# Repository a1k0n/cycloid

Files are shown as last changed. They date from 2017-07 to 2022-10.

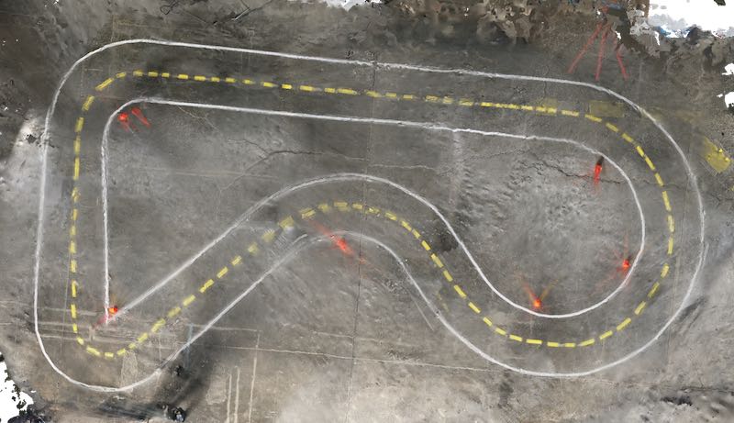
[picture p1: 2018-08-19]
design/coneslam/trackmap.jpg

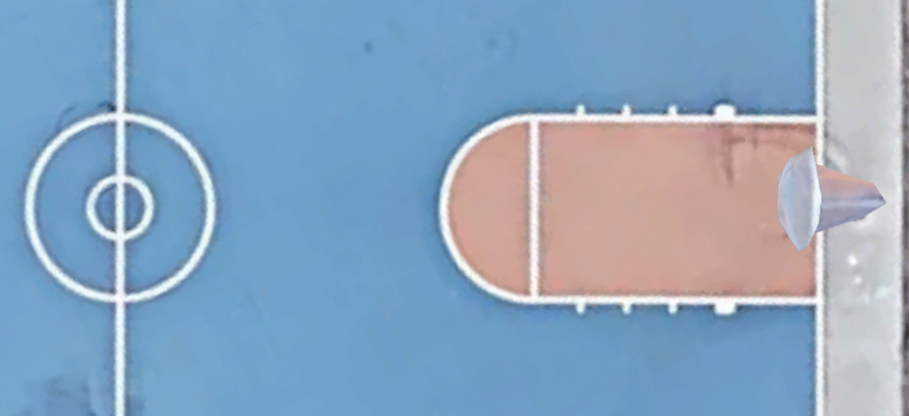
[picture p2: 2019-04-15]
design/trackplan/bball-2cm.png

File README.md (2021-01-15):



Self-racing robot using either ceiling lights or traffic cones to localize.
Very much a work in progress and documentation will always be severely
lacking as this is a constantly moving target!

This is my ongoing entry in the quarterly [DIY Robocars
competition](https://diyrobocars.com/") in Oakland, CA.

Cycloid at CircuitLaunch in Oakland (https://www.youtube.com/watch?v=vWJduGcik6Q)

## Hardware (updated!)

I've switched to a 1/10th scale touring car (for flat ground courses) as it
handles much better and also eliminates the very finicky wheel encoders used on
the Rustler.

Touring car:

 - HobbyKing Blaze R2 ($99)
 - Turnigy TrackStar 9.5T sensored brushless motor 4120KV ($34)
 - Turnigy TrackStar 80A brushless sensored ESC ($40)
 - TrackStar TS-411MG digital servo ($17)
 - Basher 6600mAh 2S2P 40C hardcase LiHV pack ($38) (smaller batteries are
   fine, but I like being able to run the computer all day on one charge)
 - Tires appropriate for track (Schumacher Racing SST Mini Pins are the way to go on carpet)

Electronics:

 - Raspberry Pi 3 B ($35)
 - SanDisk Ultra 32GB microSDHC UHS-I Card ($9) -- it's important to have the
   right kind of SD card or it won't keep up with recordings, and it's hard to
   tell ahead of time which ones will work.
 - Arducam OV5647 Raspberry Pi 3 camera with LS-40180 fisheye lens ($30)
 - ILI9340 SPI 240x320 LCD display, via the fbtft device driver (about $7)
 - Some XT60 plugs and an extra 6-wire brushless sensor cable (~$10)
 - Logitech F710 wireless game pad w/ USB dongle (~$40)
 - Custom HAT board w/ STM32F030 and ICM-20600 IMU: https://easyeda.com/a1k0n/cycloid (PCB +
   parts is about $5 apiece in qty 10 from JLPCB / LCSC, plus you have to
   solder it all together)

Total hardware cost for the car comes to under $350, plus the cost of the
wireless controller (~$40).

### 3D printed mounting parts

Besides the RC car, there are three 3D-printed parts to mount the camera and
electronics for various cars (Blaze R2, Traxxas Rustler, Exceed Magnet,
WLToys K989). I drill and tap 2.5mm screw holes in most of them. These are
all modeled in OpenSCAD and source code and .stl files are in `hw/scad/`.

### Configurations

There is a mandatory configuration file called `cycloid.ini` which allows you
to specify the mode of communication to the ESC and servos (Cycloid HAT
board, GPIO pins supported; code also exists for Teensy and PCA9685) as well
as specify which IMU (all Invensense MPU-9x50, MPU-6050, ICM-2060x supported)

See `cycloid.ini.example` for full details.

### Defining a race track

 - `tools/ceilslam` has code to turn a datalog saved from the car into a
 birds-eye view of the track based on ceiling light tracking and reprojecting
 the pixels which can see the floor.

 - `tools/trackplan/gui.py` contains a Dear Imgui-based application for
 defining a racetrack boundary (and cone locations) given a birdseye view of
 the track. It can also get a birdseye view of the track given two different
 views and matching sets of points.

## Code

Can be compiled on a host PC with a cross compiler (e.g. on macOS you can
install this: https://www.jaredwolff.com/toolchains/) or on the Raspberry Pi
itself.

If you want to build the code, clone with `git clone --recursive
https://github.com/a1k0n/cycloid` in order to get the Raspberry Pi userland
submodule (otherwise just run `git submodule init` and `git submodule update`).

Here's how I build it:

Once you have a raspberry pi cross compiler (see two paragraphs above), edit
`crosscompile.cmake` to point to the correct compiler name / path, and do this:

```
$ mkdir build
$ cd build
$ cmake -DCMAKE_TOOLCHAIN_FILE=../crosscompile.cmake ../src -DCMAKE_BUILD_TYPE=RelWithDebInfo
$ make -j4
```

The main executable will be in `build/drive/drive`; scp that to your raspberry
pi on the car, create a `cycloid.ini`, pair a joystick, and run it.

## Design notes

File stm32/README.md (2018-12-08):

# Cycloid STM32 code

This code was mostly generated by the STM32CubeMX utility; the actual code that
does anything is in Src/main.c.

This code is for the Cycloid HAT board: https://easyeda.com/a1k0n/cycloid

It exposes an I2C device on address 0x75 and is also available via the serial
port; in fact, it will send a heartbeat on the serial port every 10ms, just as
it generates the PWM pulse for the servo and speed controller. This way, a
control loop on the Raspberry Pi can be synchronized with the actual pulses
sent to the car hardware.

## Compiling the code

Install `arm-none-eabi-gcc` on your host platform and type `make`. Copy
build/cycloidp1.1.elf to the Pi and you can flash it right on there.

## Flashing the code

The Raspberry Pi can reflash the code on the HAT using
[OpenOCD](http://openocd.org/). Raspbian has an `openocd` package, but it isn't
new enough to work using the Pi's own GPIO pins. Adafruit has a [guide to
compiling
OpenOCD](https://learn.adafruit.com/programming-microcontrollers-using-openocd-on-raspberry-pi/compiling-openocd)
which will get you up to speed. Once you have it installed, use the
`openocd.cfg` here (or modify it for your needs; it's looking for
`cycloidp1.1.elf` in the current working directory) and `sudo openocd -f openocd.cfg`. If you see
```
...

** Verify Started **
verified 8348 bytes in 0.035556s (229.282 KiB/s)
** Verified OK **
adapter speed: 1001 kHz
Info : Listening on port 6666 for tcl connections
Info : Listening on port 4444 for telnet connections
```

then it worked, and you can hit ^C, or if you really want to you can connect up
gdb and poke around.

## I2C addresses

`i2cdump 1 0x75` will show the "registers" exposed by the I2C slave; the first
three addresses can be written to. The `i2cset` / `i2cget` utilities also work.

| Address | Datatype | Function | Read/write |
|-|-|-|-|
| 0x00 | uint8 | Bits 0 and 1 are the red and green LEDs | R/W |
| 0x01 | int8 | Servo position, (-128..127) | R/W |
| 0x02 | int8 | Speed controller position, (-128..127) | R/W |
| 0x03-0x04 | uint16 little-endian | Cumulative motor encoder ticks | R |
| 0x05-0x06 | uint16 little-endian | Motor period, microseconds per tick or 0 if stopped | R |

There are three "encoder ticks" per motor revolution (it's counting the falling
edge of each of the three motor phase windings).

Cumulative encoder ticks wraps at 65536, naturally; just subtract the previous
reading from the current one to get the number of ticks since last reading.
This can be used to determine distance travelled (divide by 3\*total gear ratio,
multiply by wheel circumference).

Motor period gives you the inverse motor velocity; if the field is nonzero,
divide 1000000 / period to get velocity in ticks/second.

## Serial format

The serial protocol sends a 6-byte packet every 10ms at 115200 baud, 8 data
bits, 1 stop bit, no parity:

| Offset | Value | Description |
|-|-|-|
| 0 | 0xAA | sync marker |
| 1-2 | motor encoder ticks (uint16le) | same as address 0x03-0x04 from I2C registers |
| 3-4 | motor encoder period (uint16le) | same as address 0x05-0x06 from I2C registers |
| 5 | checksum | one's complement of sum of bytes 0..4 |

It accepts 5-byte packets:

| Offset | Value | Description |
|-|-|-|
| 0 | 0x55 | Sync marker |
| 1 | LED flags | same as address 0x00 in I2C registers |
| 2 | servo position (int8) | same as address 0x01 |
| 3 | ESC position (int8) | same as address 0x02 |
| 4 | checksum | one's complement of sum of bytes 0..3 |

If the receiver's checksum doesn't match, it will respond with 0xFE (if it was
not already transmitting a packet; otherwise it will silently ignore the input)

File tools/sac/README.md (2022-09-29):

# soft actor-critic implementation for diyrobocars

trains 2x *Q* networks and one &pi; network.

the network architecture has an embedding layer like a language model has; one
*d*-dim vector for each point on the track. Track data is a side input
containing x, y of centerline and unit vector pointing forward along the track.
The Circuit Launch track this was initially trained on has 315 points,
subdivided roughly equidistantly from an SVG drawing.

So each little spot on the track is kind of like a token in a language model,
so that the network can learn the optimal way through the track at that
particular spot.

The embedding is added to the local state [x, y in local track frame, sin/cos
of direction in local track frame, velocity, yaw rate] projected through a
linear layer.

```
 [state vector]                              [action (Q network only)]
----------------                                 ---------------
| linear 6 x H |      [track embedding, dim=H]   | linear 2 x H|
       |                        |                   |
       `----------(+)-----------'-------------(+)---'
                   |
            |Mish activation|
                   |
            |   HxH linear  |
                   |
            |Mish activation|
                   |
         .-----------------------------------.
         |                |                  |
   | linear Hx2 |   | linear Hx2 |     | linear Hx1 |
      action mu     action logstd          Q value
  |-------pi network only--------|  |-Q networks only-|
```

The *Q* network has 128 hidden dimensions; the &pi; network has 16.

So basically, I just add the track embedding to the projection of the state
(/action as applicable), mish activation, run it through a fully-connected
layer, another mish activation, then a linear projection to get actions or Q
values. The architecture is extremely simple because the control policy is
locally extremely simple; the embedding layer contains all the information on
the best racing line.

There is an alternative, more general way to do this that wouldn't be
map-specific, which is to feed the future curvature information into the
network as an input.

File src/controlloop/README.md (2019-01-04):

this code uses the new serial interface to the STM32F030 HAT board to make a
lock-step 100Hz control loop.

experimental only for now; will roll this into drive/ soon.

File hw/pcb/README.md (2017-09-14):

This is a PCB which carries the Teensy 3.2 and connects to the servo & speed
controller on the car, as well as the stock R/C radio, wheel encoders, and an
analog feedback tap from the servo's internal potentiometer (requires modifying
servo).

It has the same mounting holes as the PCA9685 I2C PWM expander board commonly
used for the purpose of connecting a Raspberry Pi to an R/C car.

It can be seen (and purchased) here: 


<br>
<a href="https://oshpark.com/shared_projects/DP0wzTcU">order on OSHPark</a>

(Note that I have a ton of extras; if you ask me at an Oakland DIYRobocars race
I'll give you one)

It also has an i2c piggyback connection for the IMU.

R1 and R2 are pull-up resistors for I2C; I do not recommend populating them,
however.

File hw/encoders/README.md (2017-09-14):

Wheel encoders are jleichty's design:

http://www.blargh.co/2013/12/rc-car-quadrature-wheel-encoders.html

Except I'm only using one of the two encoder channels on each wheel, as I
assume wheels only go forwards.

PCBs are available at https://www.oshpark.com/profiles/jleichty

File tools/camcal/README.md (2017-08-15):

I use a 170 degree fisheye camera (this model:
https://www.amazon.com/dp/B01FR03MGG )

so this is a fisheye calibration

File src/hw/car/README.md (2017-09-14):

Interfacing code with RC car components.

Supports PCA9685 (not currently used) and a Teensy communicating via I2C,
running the code in the `arduino` code directory at the top level of this
repository.

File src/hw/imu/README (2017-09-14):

IMU is 3 devices on i2c (/dev/i2c-1):

address map:
0x68: ITG3200 3-axis gyro
0x1e: HMC5883L 3-axis compass
0x53: ADXL345 3-axis accelerometer

ITG3200 gyro:
16 DLPF_FS -> set to 0x18 + 0..6,
  0=256Hz bw / 8kHz samplerate,
 ... all 1kHz after this
  1=188Hz bw / 1kHz samplerate,
  2=98Hz bw  / 1kHz samplerate,
  5=10Hz,
  6=5Hz bw
1D GYRO_XOUT_H
1E GYRO_XOUT_L
1F GYRO_YOUT_H
20 GYRO_YOUT_L
21 GYRO_ZOUT_H
22 GYRO_ZOUT_L
no fifo, but an interrupt pin.  hmm.  not sure if there's any way to tell if
there's new data without using the interrupt pin, but a 1kHz samplerate is
really fast; we'll have to set the bandwidth and assume our own samplerate

ADXL345 accelerometer:
0x2c - bw_rate - defaults to 0x0a, 100Hz, 50Hz bandwidth
 0x07 - 12.5Hz samplerate, 6.25Hz bw
 0x08 - 25Hz samplerate, 12.5Hz bw
0x2d - power_ctl - need to enable measure bit to turn on; set to 0x08
0x31 — DATA_FORMAT - 0x08 - set FULL_RES
32 X-Axis data 0
33 X-Axis data 1
...
37 Z-Axis data 1

this chip has a FIFO; how to use it?

HMC5883L compass:
0x00 - CRA - controls output rate and number of averaged samples
0x01 - CRB - upper 3 bits control gain, 0xe0 least gain, 0x00 most, 0x20 default
 -- need to do some sort of AGC here to try to figure out compass direction, though local magnetic fields might just throw it off completely, especially from our motor
0x02 - mode register - 0x00 for continuous measurement
0x03:04 - x (towards pins 5-8) msb:lsb
0x05:06 - z (up) msb:lsb
0x07:08 - y (towards pins 9-12) msb:lsb
0x09 - status - bit 0 set if new data

---

our motion model:

three modes of motion:
 - A: on the ground, full traction (or slight understeer?)
 - B: on the ground, rear-wheel skidding
 - C: off the ground, i.e. jumping off a ramp
   - unlikely unless we experienced a vertical acceleration beforehand, and are experiencing 0g vertical now

basic motion model:
 - use verlet integration
 - servo position estimate <- pwm
 - yaw rate <- kalman filter(servo position estimate, lateral accel, gyro, compass)
 - orientation += yaw rate
 - motor speed estimate <- pwm
 - velocity <- kalman filter(motor speed estimate, straight accel, gps)
 - position <- kalman filter(velocity estimate, gps)
something like that?

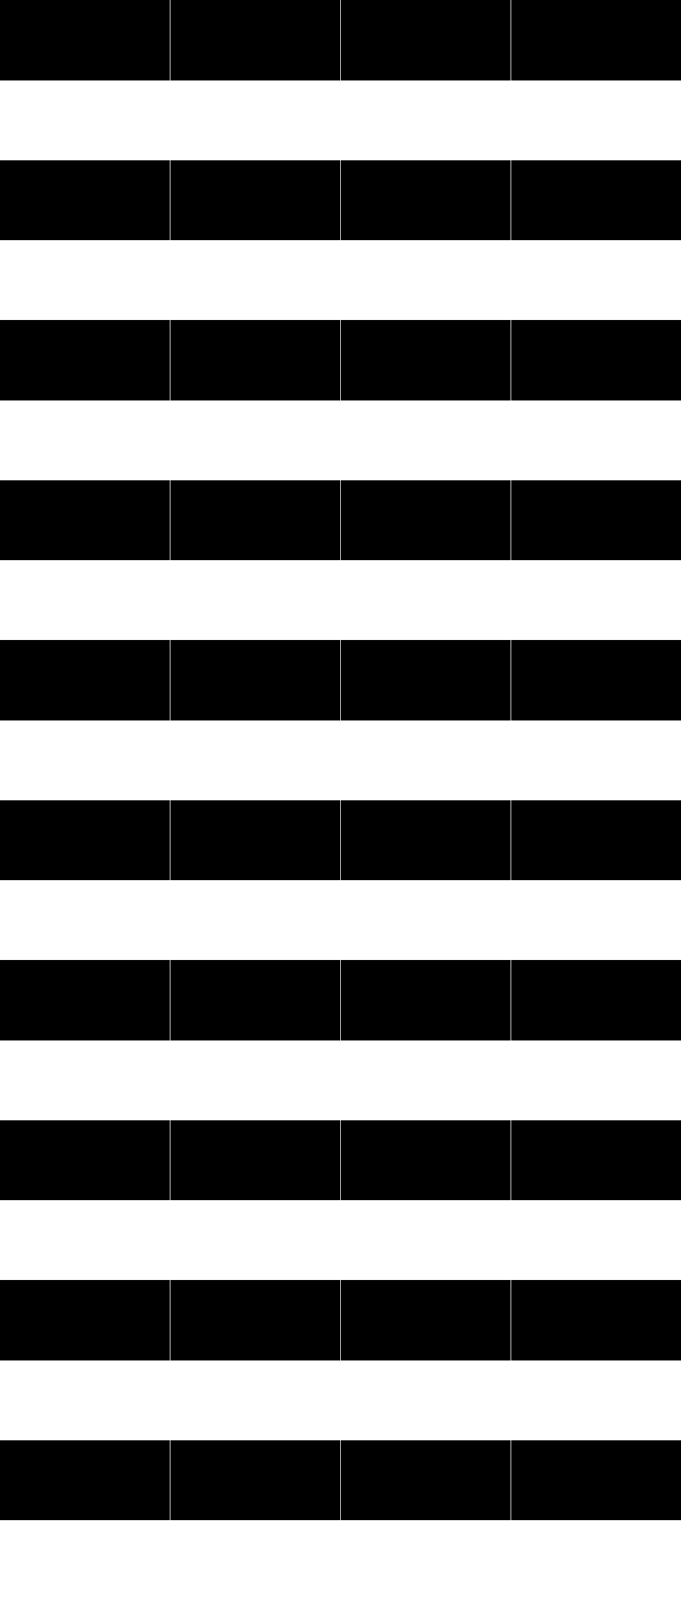
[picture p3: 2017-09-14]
hw/encoders/wheelencoder.png

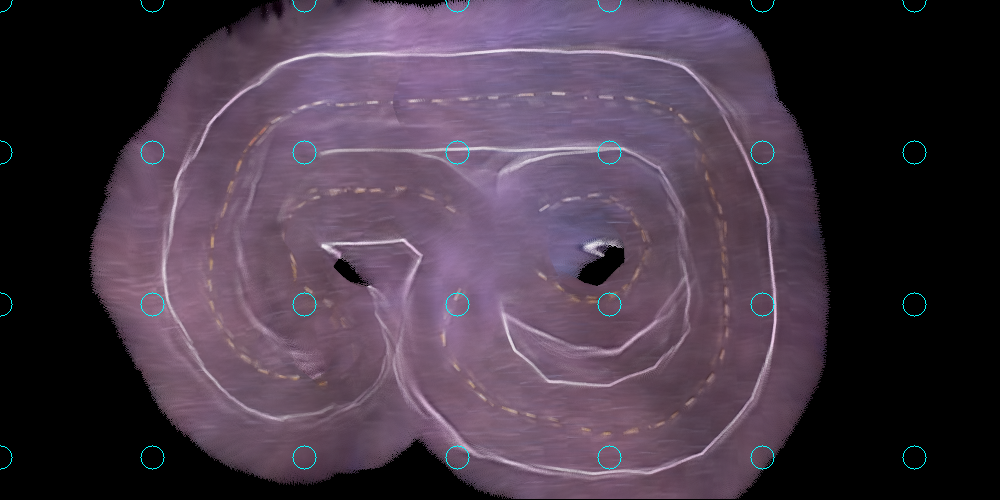
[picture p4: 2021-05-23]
tools/ceilslam/map.png

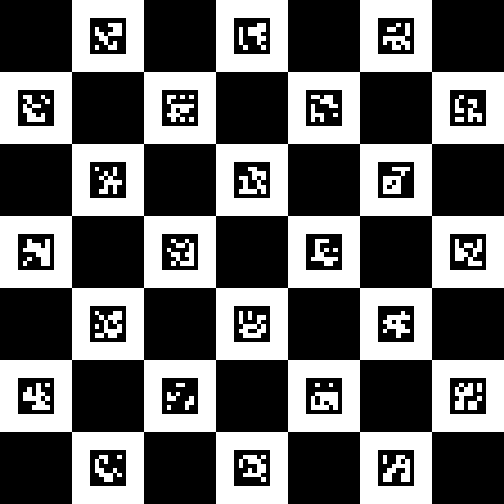
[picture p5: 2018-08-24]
tools/camcal/calboard.png

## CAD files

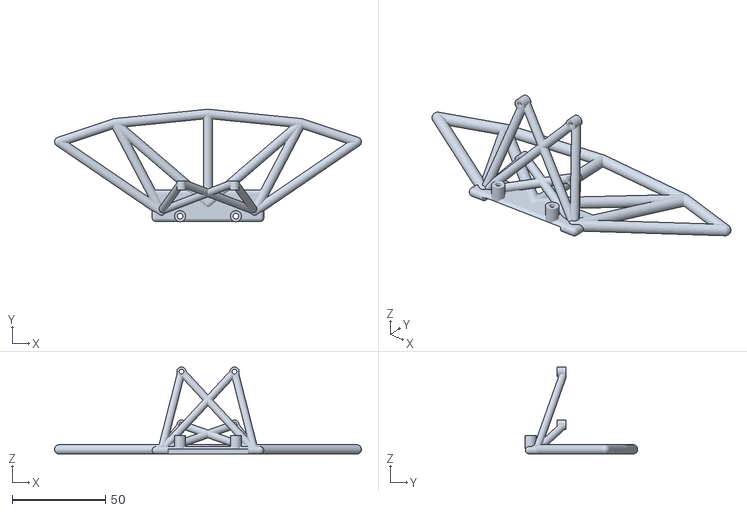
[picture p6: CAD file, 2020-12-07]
hw/scad/qvandal-bumper.stl
165.0 x 60.5 x 46.7

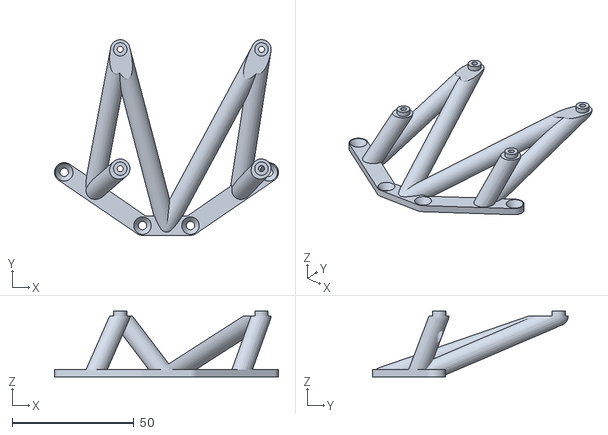
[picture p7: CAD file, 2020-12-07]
hw/scad/qvandal-rpi.stl
92.0 x 80.4 x 27.0

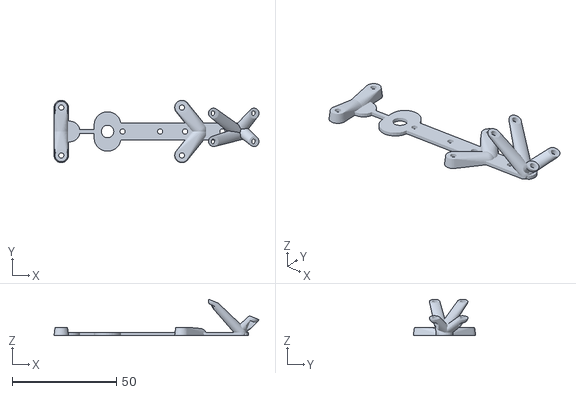
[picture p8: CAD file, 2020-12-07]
hw/scad/k989.stl
98.6 x 30.0 x 17.5

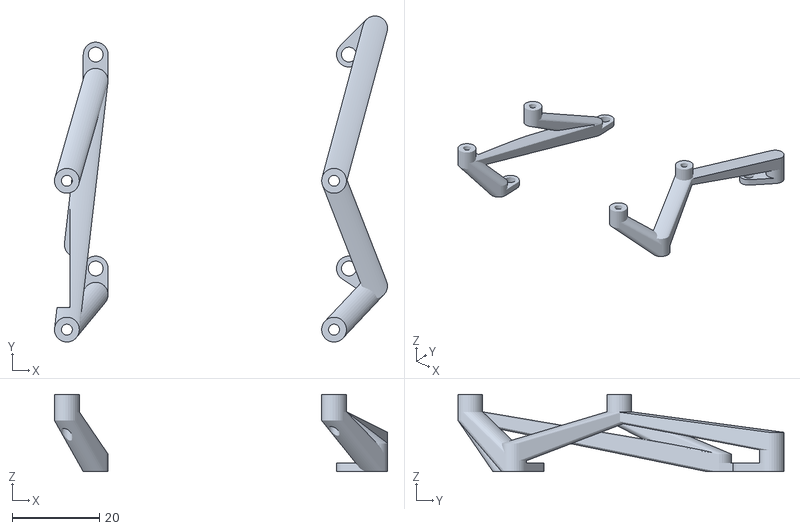
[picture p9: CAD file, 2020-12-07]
hw/scad/magnet-dispriser.stl
76.3 x 74.7 x 17.7

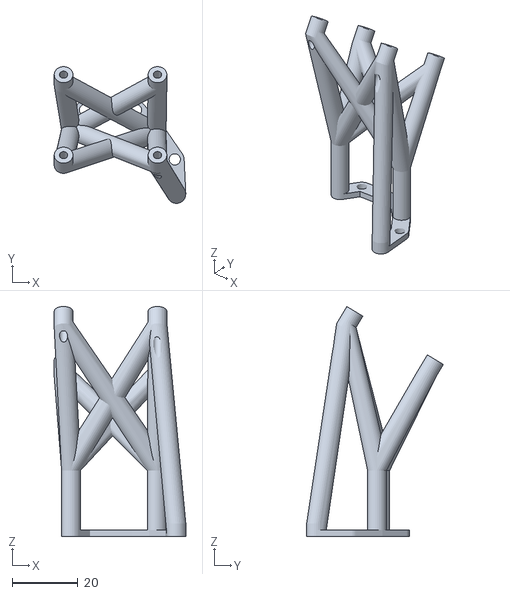
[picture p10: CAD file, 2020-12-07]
hw/scad/magnet-camera.stl
40.0 x 41.5 x 69.8

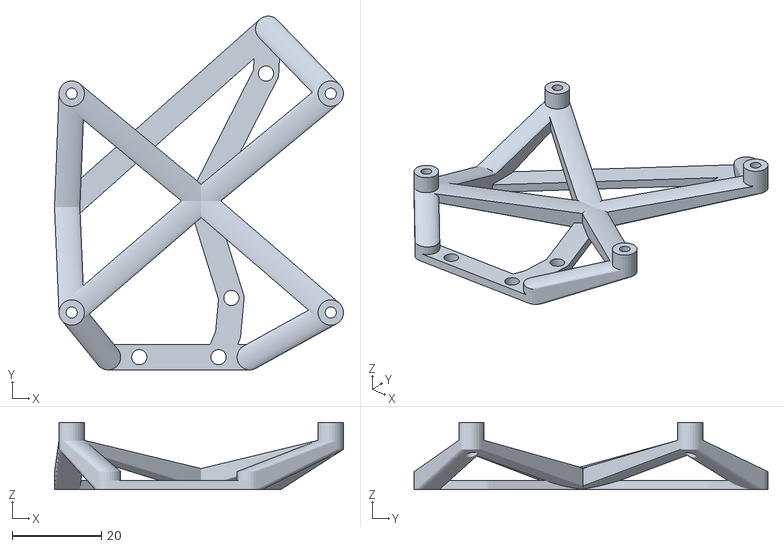
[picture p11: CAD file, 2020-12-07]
hw/scad/magnet-rpimount.stl
64.7 x 79.2 x 15.0

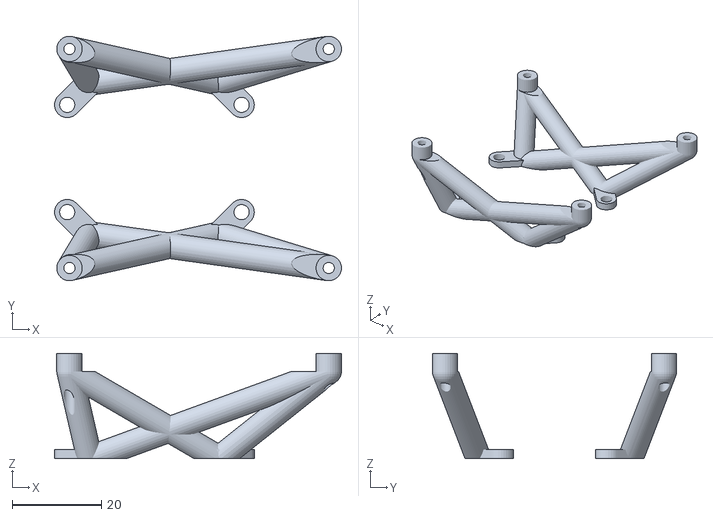
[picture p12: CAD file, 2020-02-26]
hw/scad/blazer1-rpimount.stl
64.2 x 54.7 x 23.5

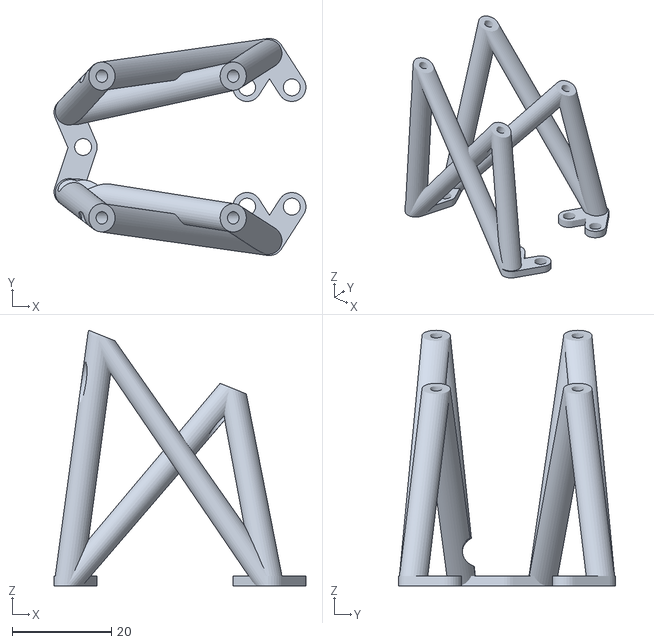
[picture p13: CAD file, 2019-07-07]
hw/scad/blazer1-windshield.stl
50.7 x 43.7 x 51.4

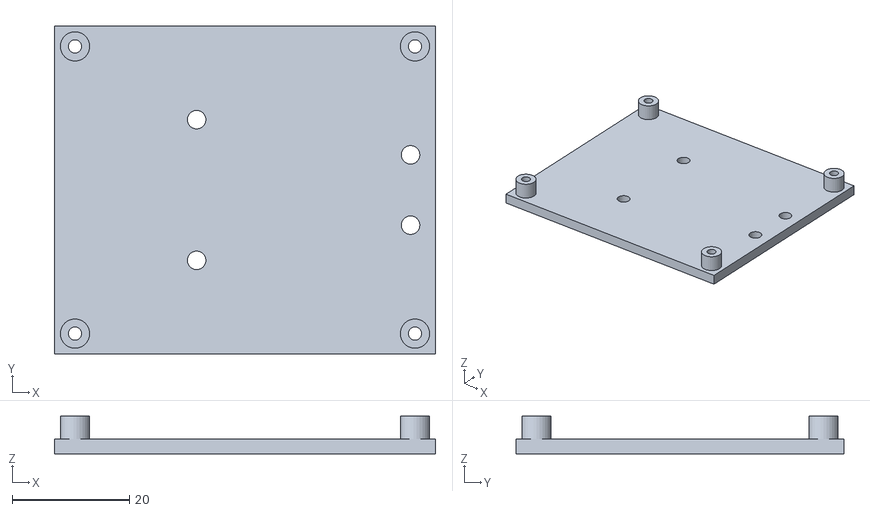
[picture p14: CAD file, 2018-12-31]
hw/scad/blazer1-baseplate-rpionly.stl
65.0 x 56.0 x 6.40

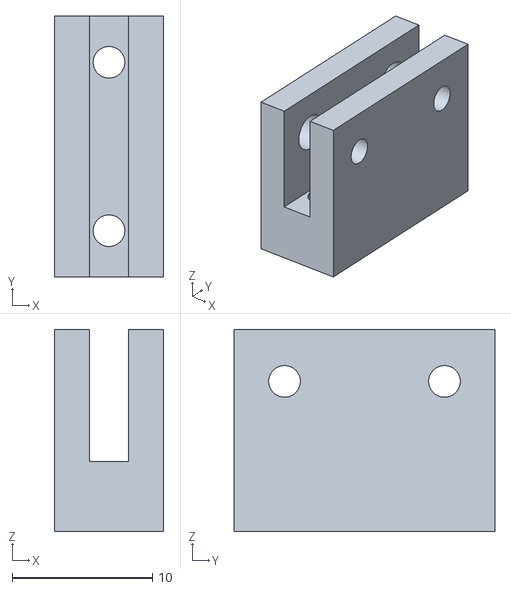
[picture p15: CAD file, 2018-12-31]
hw/scad/blazer1-shocktowermount.stl
7.80 x 18.6 x 14.4

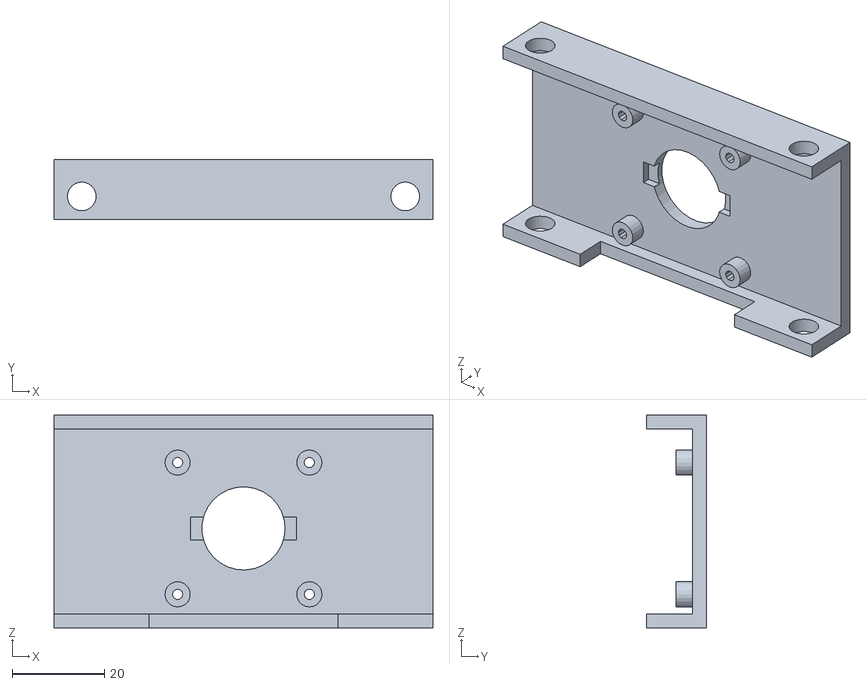
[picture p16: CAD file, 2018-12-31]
hw/scad/blazer1-arducam.stl
82.0 x 13.0 x 46.0

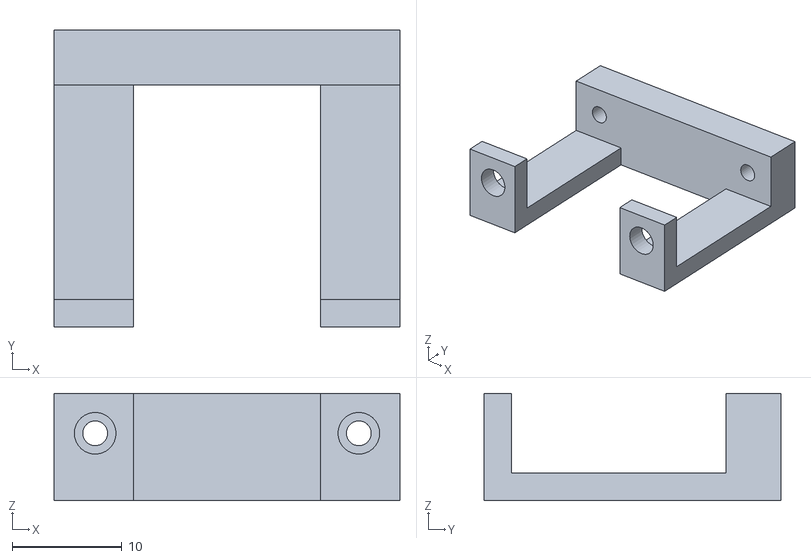
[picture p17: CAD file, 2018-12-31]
hw/scad/blazer1-sprocketmount.stl
31.5 x 27.0 x 9.76

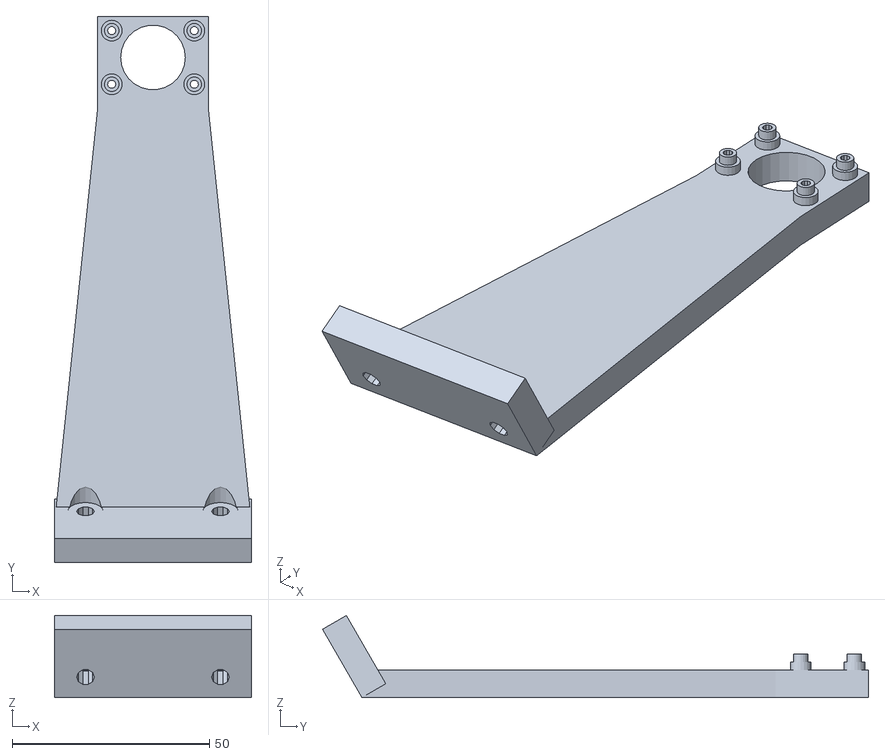
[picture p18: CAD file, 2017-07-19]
hw/scad/camholder.stl
50.0 x 138.6 x 20.8

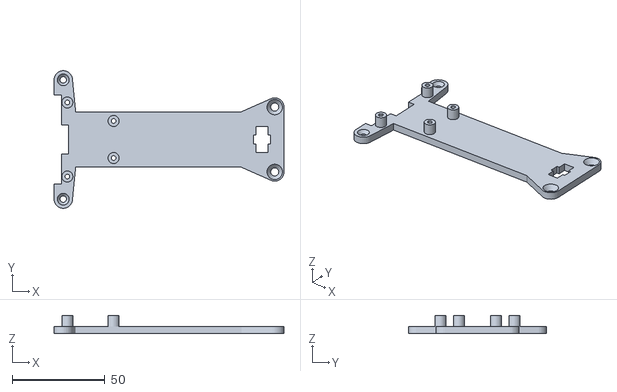
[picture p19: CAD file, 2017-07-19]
hw/scad/servoplate.stl
124.2 x 74.3 x 9.90

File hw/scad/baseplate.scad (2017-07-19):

include <fasteners.scad>
include <traxxas.scad>

$overbore = 0.25;

// All screws are #4-40, 2.2606 internal diameter
BasePlateMountingScrews = [
  [-55, 20], [-55, -20],
  [-30, 10], [-30, -10]
];

RPi3MountingScrews = [
  [3.5, 3.5], [3.5 + 58, 3.5],
  [3.5, 3.5 + 49], [3.5 + 58, 3.5 + 49]
];

PWMBoardScrews = [
  [3.3, 3.3], [59.2, 3.3],
  [3.3, 22.4], [59.2, 22.4]
];

IMUBoardScrews = [
  [2.5, 2.5], [2.5, 23]
];

PowerBoostScrews = [
  [2.6, 25], [2.6 + 17.65, 25], [2.6 + 17.65 / 2, 3]
];

module IMUMount() {
  // dimensions of 9DOF PCB
  // FIXME for MPU9250
  width = 22.1;
  length = 16.85;
  depth = 1.66;  // PCB is 1.66mm thick or so
  height = 3;  // stand off 3mm
}

module BasePlate() {
  thick = 4;
  difference() {
    union() {
      linear_extrude(thick) minkowski() {
        polygon(points = [
            [Servoplate_screws[0][0], Servoplate_screws[0][1]],
            [40, -10],
            [-55, -10],
            [Servoplate_screws[2][0], Servoplate_screws[2][1]],
            [Servoplate_screws[3][0], Servoplate_screws[3][1]],
            [-55, 10],
            [40, 10],
            [Servoplate_screws[1][0], Servoplate_screws[1][1]]]);
        circle(r=5);
      }
      for (h = BasePlateMountingScrews) {
        translate([h[0], h[1], thick-0.1])
          cylinder(d=6, h=6);
      }
    }

    for (c = Servoplate_cutouts) {
      translate([c[0], -c[1]/2, -0.01]) cube([c[2], c[1], 4.4]);
    }

    for (d = Servoplate_doohicky) {
      margin = 1;
      translate([d[0] - d[1] - margin, -d[2]/2 - margin, -0.1])
        cube([d[1] + 2*margin, d[2] + 2*margin, d[3]]);
    }

    for (s = Servoplate_screws) {
      translate([s[0], s[1], thick + 0.001]) {
        if (s[2] == 3) m3flushscrew(h=20);
        else m4flushscrew(h=20);
      }
    }

    for (h = BasePlateMountingScrews) {
      translate([h[0], h[1], -0.1])
        cylinder(d=2.2606 + $overbore, h=thick+20);
    }
  }
}

module ElectronicsPlate() {
  thick = 3;
  totalsize = [120, 90, thick];
  mounting_offset = [130, totalsize[1] / 2, 0];
  difference() {
    union() {
      translate(-mounting_offset) {
        cube(totalsize);
        translate([120, 90, 0]) rotate([0, 0, 180]) {
          for (h = RPi3MountingScrews) {
            translate([h[0], h[1], thick-0.1]) cylinder(d=5, h=5);
          }
          translate([0, 61, 0])
            for (h = PWMBoardScrews) {
              translate([h[0], h[1], thick-0.1]) cylinder(d=5, h=5);
            }
          translate([68, 61, 0])
            for (h = IMUBoardScrews) {
              translate([h[0], h[1], thick-0.1]) cylinder(d=5, h=5);
            }
          translate([88, 61, 0])
            for (h = PowerBoostScrews) {
              translate([h[0], h[1], thick-0.1]) cylinder(d=5, h=5);
            }
          translate([90, 2, 1.9]) {
            translate([0, 38, 0]) rotate([90, 0, 90]) {
              linear_extrude(height=30) polygon(points=[[0,0], [-1,0], [-1,8], [-3,10], [-2,10], [0,8]]);
            }
            rotate([90, 0, 90]) {
              linear_extrude(height=30) polygon(points=[[0,0], [1,0], [1,8], [3,10], [2,10], [0,8]]);
            }
          }
        }
      }
    }
    for (h = BasePlateMountingScrews) {
      translate([h[0], h[1], -0.1])
        cylinder(d=2.2606 + $overbore, h=thick+0.2);
    }
    translate(-mounting_offset) {
      translate([120, 90, 0]) rotate([0, 0, 180]) {
        for (h = RPi3MountingScrews) {
          // #4-40 screws
          translate([h[0], h[1], -0.1]) cylinder(d=2.2606 + $overbore, h=thick + 6);
        }
        translate([0, 61, 0])
          for (h = PWMBoardScrews) {
            // PCA9685 uses M2 screws
            // translate([h[0], h[1], -0.1]) cylinder(d=1.6 + $overbore, h=thick + 6);
            // but my replacement board is M2.5 / #4-40 screws
            translate([h[0], h[1], -0.1]) cylinder(d=2.2606 + $overbore, h=thick + 6);
          }
        translate([68, 61, 0])
          for (h = IMUBoardScrews) {
            // #4-40
            translate([h[0], h[1], -0.1]) cylinder(d=2.2606 + $overbore, h=thick + 6);
          }
        translate([88, 61, 0])
          for (h = PowerBoostScrews) {
            // M2
            translate([h[0], h[1], -0.1]) cylinder(d=1.6 + $overbore, h=thick + 6);
          }
      }
    }
  }
};

translate([0,0,-0.01]) %servoholder();
%BasePlate();
translate([0, 0, 4+6]) ElectronicsPlate();

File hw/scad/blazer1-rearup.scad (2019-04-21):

$fs = 0.05;
thickness = 2;
cam_border = 3;

rpi_mount_height = 23.5;
rpi_mount_x = -3;

cam_mount_height = 23 + 53 - 3.25;
cam_mount_x = 107;

r2 = 1.0/sqrt(2);
function rot45(x) = [x[0]*r2 + x[1]*r2, -x[0]*r2 + x[1]*r2];

arducam_width = 37;
arducam_height = 37;
arducam_mount = [
  rot45([-28.5/2, 28.5/2]),
  rot45([-28.5/2, -28.5/2]),
  rot45([28.5/2, -28.5/2]),
  rot45([28.5/2, 28.5/2]),
];
arducam_lens_diam = 18;

RPi3MountingScrews = [
  [3.5, -49.0/2], [3.5 + 58, -49.0/2],
  [3.5, 49.0/2], [3.5 + 58, 49.0/2]
];

// #4-40 sizes:
//screw_diam = ???
//screw_drill = .0890 * 25.4;  // (2.2606)
//screw_clearance = ???

screw_diam = 2.5;
//screw_drill = 2.05;
// technically it should be drilled to 2.05mm and tapped, but there's exactly
// the right amount of over-extrusion to catch screw threads if we just make a
// 2.5mm hole, with no drilling/tapping.
screw_drill = 2.5;
screw_clearance = 3.4;
screw_wall_thickness = 1.6;  // must be a multiple of nozzle size 0.4

module mountpoint(x, y) {
  translate([x, y, -2]) cylinder(d=screw_diam-0.2, h=2);
}

module CarMountingReference() {
  // Put little cylinders where all the mounting holes are in the base plate
  fork_x = [0, 8.8, 21.5, 39];
  for (x = fork_x) {
    mountpoint(x, -12);
    mountpoint(x, 12);
  }
  for (x = [75.5, 111.5, 127.5, 138.5]) {
    mountpoint(x, 0);
  }
}

module RaspiMountReference() {
  for (s = RPi3MountingScrews) {
    mountpoint(s[0], s[1]);
  }
}

module CamMountReference() {
  for (s = arducam_mount) {
    mountpoint(s[0], s[1]);
  }
}

module FrontSprocketMount() {
  height = 27;
  spacing = 24;
  thick = 2.5;
  width = spacing + 3*thick;
  x1 = 2*thick + screw_diam;
  difference() {
    union() {
      translate([-width/2, 0, 0])
        cube([width, height, thick]);
      for (side = [-width/2, width/2-x1]) {
        translate([side, 0, thick-0.1])
          cube([x1, thick, x1+0.1]);
      }
      translate([-width/2, height-2*thick, 0])
        cube([width, 2*thick, x1+thick]);
    }

    translate([-width/2+x1, -0.1, -0.1])
      cube([width-2*x1, height-2*thick+0.1, thick+0.2]);

    for (side = [-1, 1]) {
      translate([side*spacing/2, -0.1, thick+x1/2])
        rotate([-90, 0, 0])
        cylinder(d=screw_diam, h=100, $fn=30);
      translate([side*spacing/2, -0.1, thick+x1/2])
        rotate([-90, 0, 0])
        cylinder(d=3.8, h=thick*3, $fn=30);
    }

  }
}

module beam_flat(p0, p1, r) {
  dx = p1[0] - p0[0];
  dy = p1[1] - p0[1];
  dz = p1[2] - p0[2];
  M = [
    [1, 0, dx/dz, 0],
    [0, 1, dy/dz, 0],
    [0, 0, 1, 0],
    [0, 0, 0, 1]
  ];
  translate(p0) multmatrix(M) cylinder(h=dz, r=r);
}

module beam(p0, p1, r) {
  dx = p1[0] - p0[0];
  dy = p1[1] - p0[1];
  dz = p1[2] - p0[2];
  intersection() {
    hull() {
      translate(p0) sphere(r=r);
      translate(p1) sphere(r=r);
    }
    translate([
        min(p0[0], p1[0]) - r,
        min(p0[1], p1[1]) - r,
        min(p0[2], p1[2])])
      cube([abs(dx)+2*r, abs(dy)+2*r, abs(dz)]);
  }
}

module OffsetMount(p0, p1, r) {
  difference() {
    linear_extrude(height=thickness) {
      hull() {
        translate(p0) circle(r=r);
        translate(p1) circle(r=r);
      }
    }
    translate([p0[0], p0[1], -0.1]) cylinder(d=screw_clearance, h=thickness+0.2);
  }
}

module RpiBoardThing() {
  r = screw_wall_thickness + screw_drill/2;
  o=5;
  stand = 4;

  beam_size = r;

  OffsetMount([0, -12], [0+o, -12-o], r);
  OffsetMount([39, -12], [39-o, -12-o], r);
  OffsetMount([0, 12], [0+o, 12+o], r);
  OffsetMount([39, 12], [39-o, 12+o], r);

  difference() {
    h = rpi_mount_height - stand;
    union() {
      for (i = [0, 1]) {
        beam([0+o, -12-o, 0], [rpi_mount_x + RPi3MountingScrews[i][0], RPi3MountingScrews[i][1], h], beam_size);
        beam([39-o, -12-o, 0], [rpi_mount_x + RPi3MountingScrews[i][0], RPi3MountingScrews[i][1], h], beam_size);
      }
      for (i = [2, 3]) {
        beam([0+o, 12+o, 0], [rpi_mount_x + RPi3MountingScrews[i][0], RPi3MountingScrews[i][1], h], beam_size);
        beam([39-o, 12+o, 0], [rpi_mount_x + RPi3MountingScrews[i][0], RPi3MountingScrews[i][1], h], beam_size);
      }
      for (s = RPi3MountingScrews) {
        translate([rpi_mount_x + s[0], s[1], rpi_mount_height - stand - 0.1])
          cylinder(r=r, h=stand+0.1);
      }
    }
    for (s = RPi3MountingScrews) {
      translate([rpi_mount_x + s[0], s[1], rpi_mount_height - 20])
        cylinder(d=screw_drill, h=20.1);
    }
  }
}

module CamBoardThing() {
  r = screw_wall_thickness + screw_drill/2;
  offpts = [[80, 7, 0], [111.5, 7, 0], [133, 7, 0]];

  beam_size = r;

  // the belt travels along the -y side, so offset by 2mm to give it extra room
  function otherside(p) = [p[0], -p[1]-2, p[2]];

  OffsetMount([75.5, 0], offpts[0], r);
  OffsetMount([75.5, 0], otherside(offpts[0]), r);
  OffsetMount([111.5, 0], offpts[1], r);
  OffsetMount([111.5, 0], otherside(offpts[1]), r);
  OffsetMount([127.5, 0], offpts[2], r);
  OffsetMount([127.5, 0], otherside(offpts[2]), r);
  OffsetMount([138.5, 0], offpts[2], r);
  OffsetMount([138.5, 0], otherside(offpts[2]), r);

  difference() {
    union() {
      for (p0 = offpts) {
        for (p1 = arducam_mount) {
          p = p0;
          if (p1[1] > -20) {
            beam(p0, [p1[0] + cam_mount_x, p1[1], cam_mount_height-3], beam_size);
          } else {
            beam(otherside(p0), [p1[0] + cam_mount_x, p1[1], cam_mount_height-3], beam_size);
          }
        }
      }
      for (p1 = arducam_mount) {
        translate([p1[0] + cam_mount_x, p1[1], cam_mount_height - 3.1])
          cylinder(h=3.1, r=r);
      }
    }
    // cut screw holes
    for (p1 = arducam_mount) {
      translate([p1[0] + cam_mount_x, p1[1], cam_mount_height - 20.1])
        cylinder(h=20.2, d=screw_drill);
    }
    // make extra room for the belt
    translate([0, -6, 3.0]) rotate([0, 88, 0]) cylinder(r=3, h=200);
  }
}

%CarMountingReference();
%translate([rpi_mount_x, 0, rpi_mount_height]) RaspiMountReference();
%translate([cam_mount_x, 0, cam_mount_height]) CamMountReference();

RpiBoardThing();
CamBoardThing();

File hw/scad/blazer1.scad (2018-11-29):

thickness = 3;
cam_border = 3;
arducam_width = 37;
arducam_height = 37;
arducam_mount = [
  [-28.5/2, 28.5/2],
  [-28.5/2, -28.5/2],
  [28.5/2, -28.5/2],
  [28.5/2, 28.5/2],
];
arducam_lens_diam = 18;
screw_diam = 2.26;  // #4-40
screw_wall_thickness = 1.6;  // must be a multiple of nozzle size 0.4
support_offset = 3.5;
body_post_hole_dia = 6.5;

module FrontPostMount() {
  totalhigh = arducam_height + cam_border*2;
  difference() {
    union() {
      translate([-82/2, -10/2, 0])
        cube([82, 13, thickness]);
      translate([-82/2, 5, 0])
        cube([82, thickness, totalhigh]);
      translate([-82/2, -10/2, totalhigh])
        cube([82, 13, thickness]);
      for (h = arducam_mount) {
        translate([h[0], 5, totalhigh/2 + h[1]]) {
          rotate([90,0,0])
            cylinder(d=screw_diam + 2*screw_wall_thickness, h=support_offset + 0.1, $fn=20);
        }
      }
    }

    // front post holes
    translate([-70/2, 0, -0.1])
      cylinder(d=body_post_hole_dia, h=100, $fn=30);
    translate([70/2, 0, -0.1])
      cylinder(d=body_post_hole_dia, h=100, $fn=30);

    translate([-arducam_width/2-2, -5.1, -0.1])
      cube([arducam_width+4, 7, thickness+1]);
    translate([-23/2, 2.5, totalhigh/2 - 5/2])
      cube([23, 4.2, 5]);
    for (h = arducam_mount) {
      translate([h[0], -5, totalhigh/2 + h[1]]) {
        rotate([-90,0,0])
          cylinder(d=screw_diam, h=thickness + 11, $fn=10);
      }
    }
    // hole for lens
    translate([0, 0, totalhigh/2])
      rotate([-90,0,0])
      cylinder(d=arducam_lens_diam, h=100);
  }
}

module ShockTowerAdapter() {
  t1 = 5;  // vertical thickness
  t2 = 2.5; // thickness around CF shock tower
  t3 = 2.8;  // thickness of gap for CF shock tower
  l1 = 18.6;  // length along CF shock tower
  difference() {
    union() {
      translate([-t3/2-t2, -l1/2, 0])
        cube([t3+t2*2, l1, 9.4+t1]);
    }
    // remove gap for shock tower
    translate([-t3/2, -l1/2-0.1, -0.1])
      cube([t3, l1+0.2, 9.5]);

    // holes for screws on top
    for (side = [-1, 1]) {
      translate([0, 12*side/2, 0])
        cylinder(d=screw_diam, h=9.4+t1+0.1, $fn=30);
    }

    // screw holes going through
    for (side = [-1, 1]) {
    translate([-50, side*11.4/2, 9.4-5.7])
      rotate([0, 90, 0])
      cylinder(d=screw_diam, h=100, $fn=30);
    translate([0, side*11.4/2, 9.4-5.7])
      rotate([0, 90, 0])
      cylinder(d=screw_diam*1.4, h=100, $fn=30);
    }
  }
}

module FrontSprocketMount() {
  height = 27;
  spacing = 24;
  thick = 2.5;
  width = spacing + 3*thick;
  x1 = 2*thick + screw_diam;
  difference() {
    union() {
      translate([-width/2, 0, 0])
        cube([width, height, thick]);
      for (side = [-width/2, width/2-x1]) {
        translate([side, 0, thick-0.1])
          cube([x1, thick, x1+0.1]);
      }
      translate([-width/2, height-2*thick, 0])
        cube([width, 2*thick, x1+thick]);
    }

    translate([-width/2+x1, -0.1, -0.1])
      cube([width-2*x1, height-2*thick+0.1, thick+0.2]);

    for (side = [-1, 1]) {
      translate([side*spacing/2, -0.1, thick+x1/2])
        rotate([-90, 0, 0])
        cylinder(d=screw_diam, h=100, $fn=30);
      translate([side*spacing/2, -0.1, thick+x1/2])
        rotate([-90, 0, 0])
        cylinder(d=3.8, h=thick*3, $fn=30);
    }

  }
}

BaseScrews =[
  [-36.5/2, 12], [-36.5/2, -12],
  [36.5/2, 6], [36.5/2, -6]
];

RPi3MountingScrews = [
  [3.5, 3.5], [3.5 + 58, 3.5],
  [3.5, 3.5 + 49], [3.5 + 58, 3.5 + 49]
];

module BasePlateWithTeensy() {
  thick = 2.5;
  standoff = 4;

  basesize = [80, 85, thick];
  mountoffset = [-10, 0, 0];  // distance from center to adjust screws

  PWMBoardScrews = [
    [3.3, 3.3], [59.2, 3.3],
    [3.3, 22.4], [59.2, 22.4]
  ];

  difference() {
    union() {
      translate(mountoffset - [basesize[0]/2, basesize[1]/2, 0]) {
        cube(basesize);
        for (s = RPi3MountingScrews) {
          translate([s[0], s[1], thick-0.1])
            cylinder(d=5, h=standoff, $fn=30);
        }
      }

      translate(mountoffset - [basesize[0]/2, -basesize[1]/2, 0]) {
        for (s = PWMBoardScrews) {
          translate([s[0], -s[1], thick-0.1])
            cylinder(d=5, h=standoff, $fn=30);
        }
      }
    }

    for (s = BaseScrews) {
      translate([s[0], s[1], -0.1])
        cylinder(d=screw_diam*1.4, h=thick+0.2, $fn=30);
    }

    translate(mountoffset - [basesize[0]/2, basesize[1]/2, 0])
      for (s = RPi3MountingScrews) {
        translate([s[0], s[1], -0.1])
          cylinder(d=screw_diam, h=thick+standoff+0.2, $fn=30);
      }

    translate(mountoffset - [basesize[0]/2, -basesize[1]/2, 0]) {
      for (s = PWMBoardScrews) {
        translate([s[0], -s[1], -0.1])
          cylinder(d=screw_diam, h=thick+standoff+0.2, $fn=30);
      }
    }
  }
}

module BasePlate() {  // raspi only, with HAT board
  thick = 2.5;
  standoff = 4;

  basesize = [65, 56, thick];
  mountoffset = [-10, 0, 0];  // distance from center to adjust screws

  difference() {
    union() {
      translate(mountoffset - [basesize[0]/2, basesize[1]/2, 0]) {
        cube(basesize);
        for (s = RPi3MountingScrews) {
          translate([s[0], s[1], thick-0.1])
            cylinder(d=5, h=standoff, $fn=30);
        }
      }
    }

    for (s = BaseScrews) {
      translate([s[0], s[1], -0.1])
        cylinder(d=screw_diam*1.4, h=thick+0.2, $fn=30);
    }

    translate(mountoffset - [basesize[0]/2, basesize[1]/2, 0])
      for (s = RPi3MountingScrews) {
        translate([s[0], s[1], -0.1])
          cylinder(d=screw_diam, h=thick+standoff+0.2, $fn=30);
      }
  }
}

// rotate([-90, 0, 0]) FrontPostMount();
//rotate([0, 180, 0]) ShockTowerAdapter();
//FrontSprocketMount();
BasePlate();

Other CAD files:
hw/scad/baseplate.stl
hw/scad/blazer1-windshield.scad
hw/scad/camholder.scad
hw/scad/fasteners.scad
hw/scad/k989.scad
hw/scad/lcdstand.scad
hw/scad/magnet-dispriser.scad
hw/scad/magnet.scad
hw/scad/qvandal.scad
hw/scad/traxxas.scad

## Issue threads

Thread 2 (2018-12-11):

Not an issue just a question

naughtyStark, 2018-12-11:
I was reading the localize.cc file and it appears that you are shifting the position of (what I think are ) trajectory points relative to the car, such that the car always stays at 0,0. Is my understanding correct? Also could you maybe give an explanation if my understanding is not correct as to what the car is doing?
Thanks.

a1k0n, 2018-12-11:
No, that's not what it's doing... can you point to the line numbers you're looking at?

localize.cc is an implementation of [Monte Carlo localization](https://en.wikipedia.org/wiki/Monte_Carlo_localization) AKA a particle filter. It has a bunch of possible locations that the car is in, and each time it senses motion from the wheel encoders / gyro it moves the particles forward with some noise, and each time it detects cones it resamples the particles based on which ones are likely to have seen the cones it saw.

naughtyStark, 2018-12-11:
Oooh. Okay. I think I got it. The reason why it felt that way was because I saw particles[i].stuff and I thought you were bundle adjusting the points every time the car moved (which seemed rather computationally expensive).

One more thing, I find your project interesting, can I keep asking questions? I made something similar last year(and actually the year before that too, the one I made last year just had better hardware. The code was more or less the same. I am working on a new version of it right now and would love to discuss things ) https://www.youtube.com/watch?v=IqyNvaG0JE0    github link : https://github.com/naughtyStark/Self-driving-car . In my case the localisation wasn't using computer vision ( like in your case ) because it is supposed to be a more "general purpose" car, i.e., it is supposed to be able to work in unstructured environments (unlike the diy-robocar tracks ) and so visual markers are not a luxury I have at hand.

Thanks,
Regards
Sidharth.

a1k0n, 2018-12-11:
Not a bundle adjustment or anything like that, but yes all the points are updated at 30Hz. Not a big deal for a raspberry pi to update 300x3 floats.

Nice work! Looks like your localization used IMU integration + GPS + optical flow sensor? I've been meaning to try out an optical flow sensor, and it's awesome to see you got one to work. One thing I can't measure very easily is lateral velocity if the car is in a drift.

Sure, keep asking questions.

naughtyStark, 2018-12-11:
Okay, I'll keep this thread alive then.

Yes I do notice the same problem of lateral drift with ArduRover as well, which is kind of what inspired me to make my project in the first place. You might also notice that it has some trajectory planning. I was trying to read your driver code but I couldn't quite figure out some parts.
Here is how my car works
1)get state
2) find the bezier curve parameters of the bezier curve that joins current position to next waypoint (the details are on the github page)
3)find the ROC of the point where the car will be 2 servo/esc cycles into the future (2 because the signal is sent out at the end of each servo cycle and it would take at least one cycle to implement things)
4) find steering angle for that ROC (compensate for yaw rate errors too) and calculate throttle on the basis of target velocity (calculated from ROC) and how much total acceleration the car is undergoing.

In your code, I can't understand how you're getting the ROC/ curvature of a point (which would be step 3 in my case)

Thanks,
Regards,
Sidharth

a1k0n, 2018-12-11:
Ah. Yes, the code in here is a disaster with no clear design, just a bunch of experiments strung together.

I do something similar to you, but instead of using bezier curves I use evenly-spaced points with precomputed curvatures (1/radius). The line to drive is computed with an offline optimization step I run in a [Jupyter notebook](http://nbviewer.jupyter.org/url/a1k0n-pub.s3-website-us-west-1.amazonaws.com/diyrobocars/trackplan_circuitlaunch.ipynb), and then just upload all the waypoints as a text file which the car reads as `track.txt`. The code to get the nearest waypoint is here: https://github.com/a1k0n/cycloid/blob/master/src/drive/trajtrack.cc.

So localization is just determining my x, y, theta, and then I find the closest point on the curve, and use the control strategy outlined at the end of [my blog post here](https://www.a1k0n.net/2018/11/13/fast-line-following.html) to determine the curvature to drive, given the relative position / angle. I compute the control for every one of my particles and take the mean.

naughtyStark, 2018-12-12:
Okay (the blog post was a good read!).

In the trajtrack.cc file, I saw something like a "look-ahead" functionality. From what I can understand, the car looks a certain number of points ahead of the closest X and Y coordinates.  However, in the blogpost you mention that the idea is to look for the maximum kappa ahead of the current position to determine the target velocity. (also I don't see lookahead_k being used anywhere in the controller.cc file). Did I misinterpret the code somewhere?

If my understanding is somewhat correct and the look ahead hasn't been implemented completely,
I would like to contribute. I will make the changes in my fork and create a pull request when it is ready(it might take a while considering my exams are going on right now and will end in by the end of December).

Thanks,
Regards,
Sidharth

a1k0n, 2018-12-12:
lookahead is used but its member variable is confusingly named `vk_`. The `TrajectoryTracker::GetTarget` method takes a lookahead parameter and outputs a &kappa; for velocity lookahead (hence `vk_`).

naughtyStark, 2018-12-13:
Okay.
I noticed that the lookahead distance was fixed. I tried making it dynamic. I have created a pull request for it.

Thanks,
Regards,
Sidharth.

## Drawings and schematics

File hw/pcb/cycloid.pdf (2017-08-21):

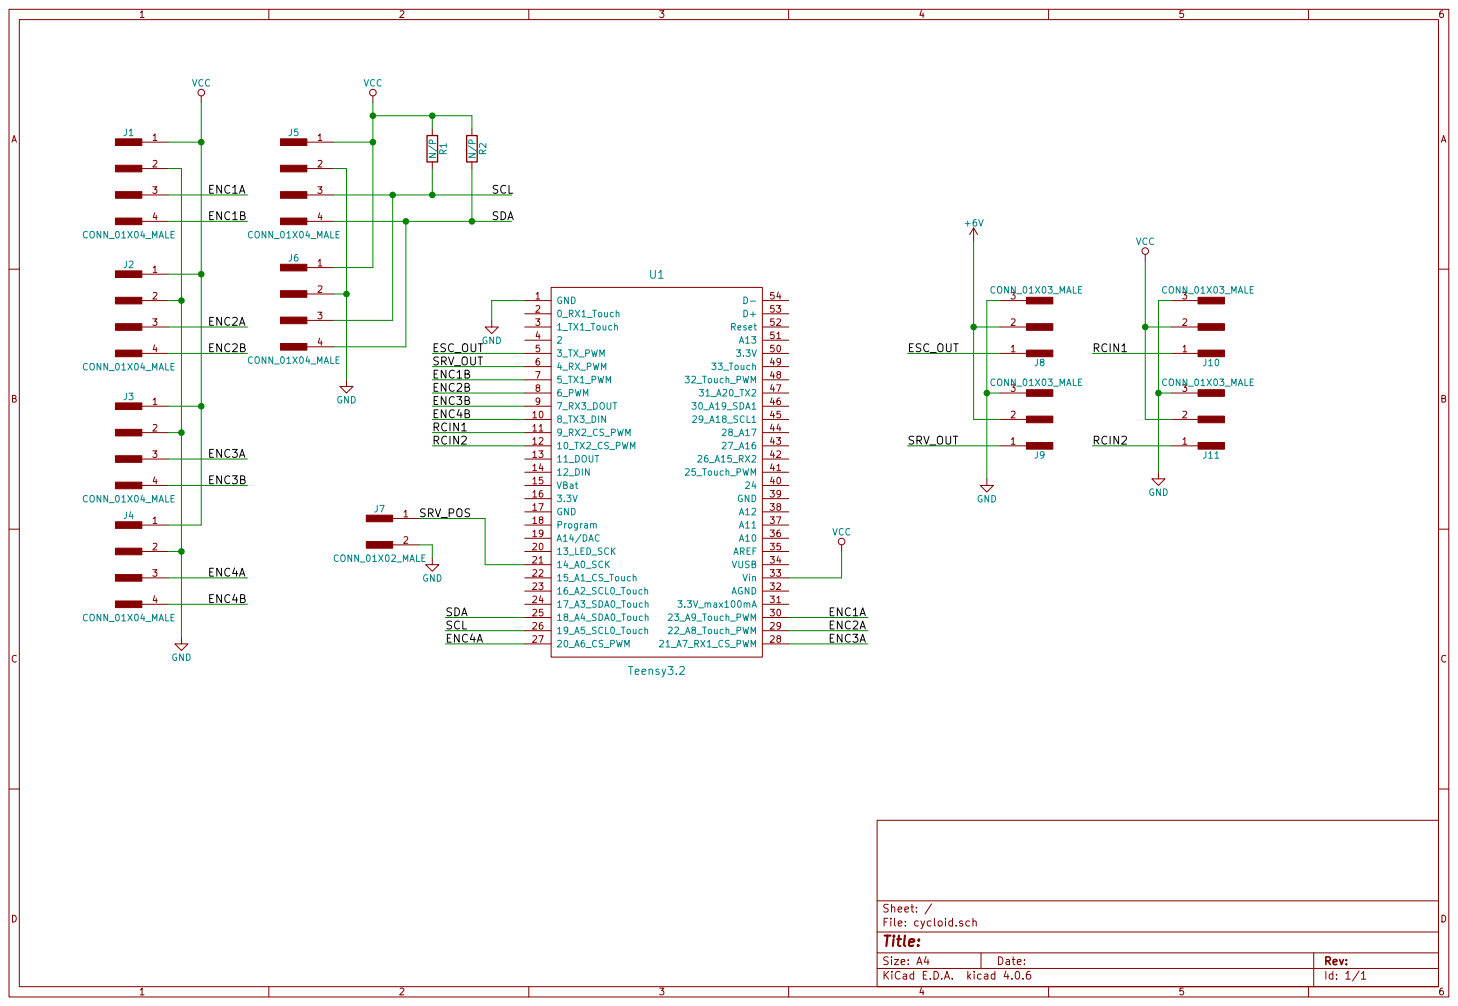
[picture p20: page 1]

File: cycloid.sch Sheet: /
Id: 1/1 Title:

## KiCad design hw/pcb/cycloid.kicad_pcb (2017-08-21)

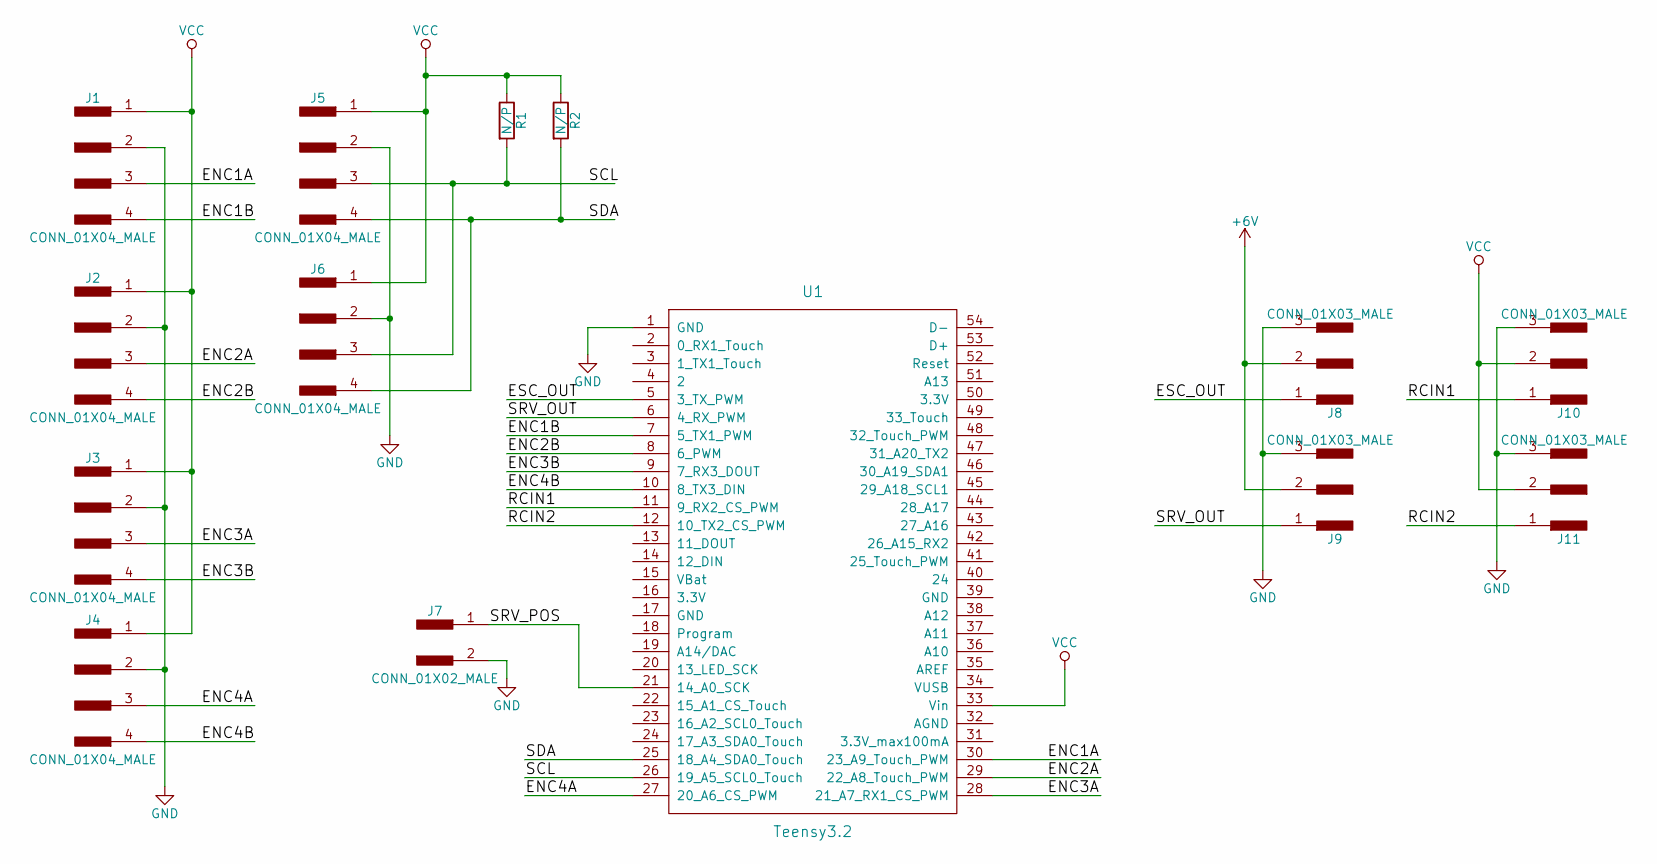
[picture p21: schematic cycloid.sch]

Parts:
J1, J2, J3, J4, J5, J6: CONN_01X04_MALE; Pin_Header_Straight_1x04_Pitch2.54mm
J7: CONN_01X02_MALE; Pin_Header_Straight_1x02_Pitch2.54mm
J8, J9, J10, J11: CONN_01X03_MALE; Pin_Header_Straight_1x03_Pitch2.54mm
R1, R2: N/P; R_0805_HandSoldering
U1: Teensy3.2; Teensy30_31_32_LC

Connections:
+6V: J8.2, J9.2
/ENC1A: J1.3, U1.30 (23_A9_Touch_PWM)
/ENC1B: J1.4, U1.7 (5_TX1_PWM)
/ENC2A: J2.3, U1.29 (22_A8_Touch_PWM)
/ENC2B: J2.4, U1.8 (6_PWM)
/ENC3A: J3.3, U1.28 (21_A7_RX1_CS_PWM)
/ENC3B: J3.4, U1.9 (7_RX3_DOUT)
/ENC4A: J4.3, U1.27 (20_A6_CS_PWM)
/ENC4B: J4.4, U1.10 (8_TX3_DIN)
/ESC_OUT: J8.1, U1.5 (3_TX_PWM)
/RCIN1: J10.1, U1.11 (9_RX2_CS_PWM)
/RCIN2: J11.1, U1.12 (10_TX2_CS_PWM)
/SCL: J5.3, J6.3, R1.2, U1.26 (19_A5_SCL0_Touch)
/SDA: J5.4, J6.4, R2.2, U1.25 (18_A4_SDA0_Touch)
/SRV_OUT: J9.1, U1.6 (4_RX_PWM)
/SRV_POS: J7.1, U1.21 (14_A0_SCK)
GND: J1.2, J2.2, J3.2, J4.2, J5.2, J6.2, J7.2, J8.3, J9.3, J10.3, J11.3, U1.1 (GND)
VCC: J1.1, J2.1, J3.1, J4.1, J5.1, J6.1, J10.2, J11.2, R1.1, R2.1, U1.33 (Vin)

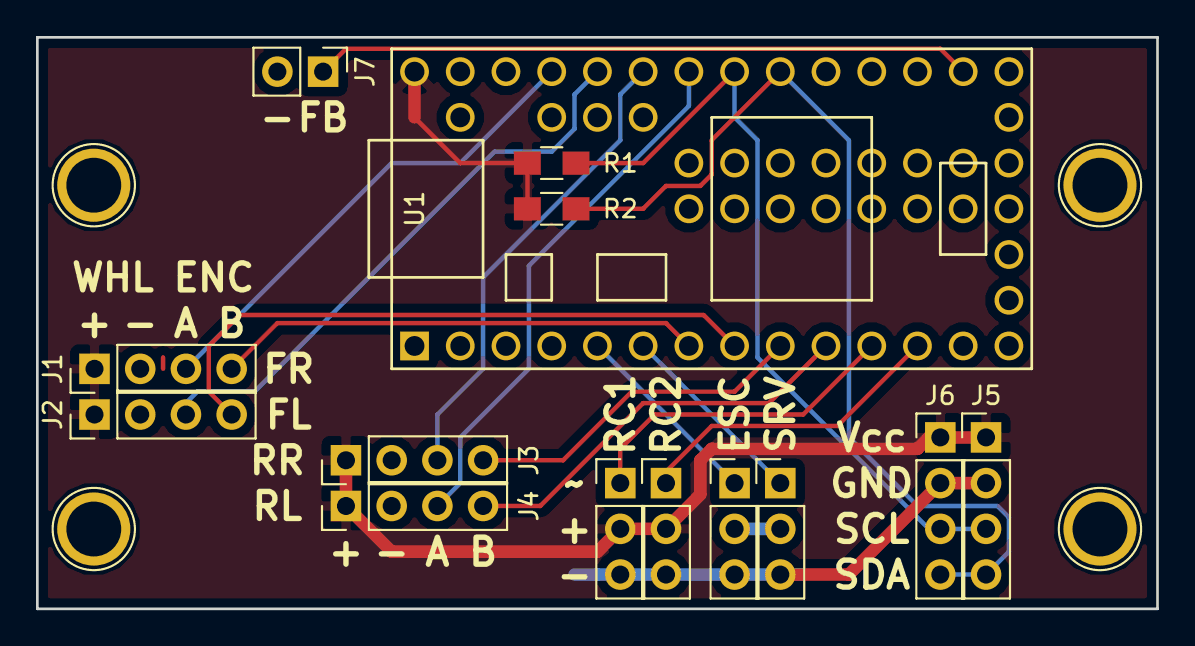
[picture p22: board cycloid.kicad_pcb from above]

Board: 2 copper layers, 62.2 x 31.7 mm, 14 parts (0 on the bottom side), 18 nets.

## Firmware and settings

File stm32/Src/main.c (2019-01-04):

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

/* Includes ------------------------------------------------------------------*/
#include "main.h"

I2C_HandleTypeDef hi2c1;

TIM_HandleTypeDef htim3;
TIM_HandleTypeDef htim14;

UART_HandleTypeDef huart1;

void SystemClock_Config(void);
static void MX_GPIO_Init(void);
static void MX_I2C1_Init(void);
static void MX_TIM3_Init(void);
static void MX_TIM14_Init(void);
static void MX_USART1_UART_Init(void);
/**
  * @brief  The application entry point.
  * @retval int
  */
int main(void)
{
  /* MCU Configuration--------------------------------------------------------*/

  /* Reset of all peripherals, Initializes the Flash interface and the Systick. */
  HAL_Init();

  /* Configure the system clock */
  SystemClock_Config();

  /* Initialize all configured peripherals */
  MX_GPIO_Init();
  MX_I2C1_Init();
  MX_TIM3_Init();
  MX_TIM14_Init();
  MX_USART1_UART_Init();
  /* USER CODE BEGIN 2 */

  HAL_TIM_PWM_Start(&htim3, TIM_CHANNEL_1);
  HAL_TIM_PWM_Start(&htim3, TIM_CHANNEL_2);
  HAL_TIM_Base_Start_IT(&htim3);
  HAL_TIM_Base_Start_IT(&htim14);
  __HAL_I2C_ENABLE_IT(&hi2c1, I2C_IT_ADDRI | I2C_IT_RXI | I2C_IT_TXI);
  SET_BIT(USART1->CR1, USART_CR1_RXNEIE);

  /* USER CODE END 2 */

  /* Infinite loop */
  /* USER CODE BEGIN WHILE */
  while (1)
  {
    /* USER CODE END WHILE */

    /* USER CODE BEGIN 3 */
    // Wait for interrupts; nothing else to do.
    __asm__("wfi");
  }
  /* USER CODE END 3 */
}

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
/* USER CODE BEGIN 4 */

static const int COMMAND_TIMEOUT = 10;  // number of 10ms intervals to expect a command
static volatile uint8_t command_timeout_ = 0;

volatile union {
  struct {
    uint8_t leds;
    int8_t esc_pwm;
    int8_t servo_pwm;
    uint16_t motor_ticks;
    uint16_t motor_period;
    uint32_t motor_last_clock;
  } __attribute__((packed));
  uint8_t bytes[16];  // must be power of 2
} i2cdata_ = {.bytes = {0}}, i2cshadow_;

// TIM14: 65536us timer interrupt
static volatile uint16_t tim14_hi = 0;
void TIM14_IRQHandler(void)
{
  if(__HAL_TIM_GET_FLAG(&htim14, TIM_FLAG_UPDATE) != RESET) {
    __HAL_TIM_CLEAR_IT(&htim14, TIM_IT_UPDATE);
    if ((i2cdata_.motor_last_clock >> 16) == tim14_hi-1) {
      // no motor activity between 65..131ms ago; consider motor stopped
      i2cdata_.motor_period = 0;
    }
    tim14_hi++;
  }
}

// TIM14 is currently configured to tick every 1us but we may want more resolution
static uint32_t get_tim14_ticks() {
  return (((uint32_t)tim14_hi) << 16) + TIM14->CNT;
}

static uint16_t pwmtiming(int8_t pwm8) {
  return 6000 + (2000*pwm8 >> 7);
}

static void update_from_i2cdata() {
  __HAL_TIM_SET_COMPARE(&htim3, TIM_CHANNEL_1, pwmtiming(i2cdata_.servo_pwm));
  __HAL_TIM_SET_COMPARE(&htim3, TIM_CHANNEL_2, pwmtiming(i2cdata_.esc_pwm));
  HAL_GPIO_WritePin(GPIOA, GPIO_PIN_5, i2cdata_.leds & 1);
  HAL_GPIO_WritePin(GPIOB, GPIO_PIN_1, (i2cdata_.leds & 2) >> 1);
  command_timeout_ = COMMAND_TIMEOUT;
}

// If we don't receive a command from the host, reset our outputs to zero so we
// don't run away
static void reset_commands() {
  __HAL_TIM_SET_COMPARE(&htim3, TIM_CHANNEL_1, pwmtiming(0));
  __HAL_TIM_SET_COMPARE(&htim3, TIM_CHANNEL_2, pwmtiming(0));
  HAL_GPIO_WritePin(GPIOA, GPIO_PIN_5, 0);
  HAL_GPIO_WritePin(GPIOB, GPIO_PIN_1, 1);
}

static void update_phase() {
  // We only really care about the speed of the motor itself, so just track
  // that instead of individual phase windings.

  uint32_t t0 = i2cdata_.motor_last_clock;
  uint32_t t1 = get_tim14_ticks();
  int32_t p = t1 - t0;

  // smooth out period readings with an adaptive filter
  // low pass, ~15Hz bandwidth
  // the filter coefficient depends on period, as we aren't updating on a fixed
  // interval but rather on period itself.

  if (p < 32768) {
    // this can overflow if |lastp - p| >= 32768 but i'm not going
    // to worry about it
    int32_t lastp = i2cdata_.motor_period;
    p += ((p*(lastp - p)) >> 16);
  }
  if (p < 65535 && p > 0) {
    i2cdata_.motor_period = p;
  } else {
    i2cdata_.motor_period = 0;
  }

  i2cdata_.motor_last_clock = t1;
  i2cdata_.motor_ticks++;
}

void EXTI0_1_IRQHandler(void) {
  int update = 0;
  if(__HAL_GPIO_EXTI_GET_IT(GPIO_PIN_0) != RESET) {
    __HAL_GPIO_EXTI_CLEAR_IT(GPIO_PIN_0);
    update = 1;
  }
  if(__HAL_GPIO_EXTI_GET_IT(GPIO_PIN_1) != RESET) {
    __HAL_GPIO_EXTI_CLEAR_IT(GPIO_PIN_1);
    update = 1;
  }
  if (update) {
    update_phase();
  }
}

void EXTI4_15_IRQHandler(void) {
  if(__HAL_GPIO_EXTI_GET_IT(GPIO_PIN_4) != RESET) {
    __HAL_GPIO_EXTI_CLEAR_IT(GPIO_PIN_4);
    update_phase();
  }
}

// I2C slave

void I2C1_IRQHandler(void) {
  // The HAL I2C slave interrupt handler stuff is all garbage; implement our own here.
  static uint8_t reg_ptr = 0;
  static uint8_t firstbyte = 0;

  uint32_t itflags = READ_REG(I2C1->ISR);
  if (itflags & I2C_FLAG_ADDR) {  // address matched; start a transfer
    __HAL_I2C_CLEAR_FLAG(&hi2c1, I2C_FLAG_ADDR);
    if (I2C_GET_DIR(&hi2c1) == I2C_DIRECTION_TRANSMIT) {
      // prepare to receive bytes from master; first byte is register number
      firstbyte = 1;
    }
  }
  if (itflags & I2C_FLAG_TXE) {  // transmit register empty; send next byte
    reg_ptr = (reg_ptr+1) & (sizeof(i2cdata_) - 1);
    I2C1->TXDR = i2cshadow_.bytes[reg_ptr];
  }
  if (itflags & I2C_FLAG_RXNE) {  // receive register not empty
    uint8_t databyte = I2C1->RXDR & 0xff;
    if (firstbyte) {
      reg_ptr = databyte;
      firstbyte = 0;
      reg_ptr &= sizeof(i2cdata_) - 1;
      // flush TX buffer and reload with new data byte

      // just to ensure we don't spuriously re-trigger the interrupt we're
      // already in; I am not sure whether this is necessary:
      __disable_irq();
      i2cshadow_ = i2cdata_;  // make a shadow copy of the data for atomic reading
      I2C1->ISR |= I2C_FLAG_TXE;  // setting TXE flushes TXDR
      I2C1->TXDR = i2cshadow_.bytes[reg_ptr];
      __enable_irq();
    } else {
      reg_ptr &= sizeof(i2cdata_) - 1;
      i2cdata_.bytes[reg_ptr++] = databyte;
      update_from_i2cdata();
    }
  }
}

static uint8_t usart_txbuf[5];
static uint8_t usart_txptr = 0;
static uint8_t usart_rxbuf[4];
static int8_t usart_rxptr = -1;

void TIM3_IRQHandler(void) {
  if (__HAL_TIM_GET_FLAG(&htim3, TIM_FLAG_UPDATE) != RESET) {
    __HAL_TIM_CLEAR_IT(&htim3, TIM_IT_UPDATE);
    usart_txbuf[4] = 0xaa;
    for (uint8_t i = 0; i < 4; i++) {
      // send motor ticks and period (4 bytes, starting at 3rd i2c register)
      usart_txbuf[i] = i2cdata_.bytes[3+i];
      usart_txbuf[4] += usart_txbuf[i];
    }
    usart_txbuf[4] = ~usart_txbuf[4];
    USART1->TDR = 0xaa;
    SET_BIT(USART1->CR1, USART_CR1_TXEIE);
    usart_txptr = 0;

    if (command_timeout_ > 0) {
      command_timeout_--;
      if (command_timeout_ == 0) {
        reset_commands();
      }
    }
  }
}

void process_serial_msg(const uint8_t *buf) {
  uint8_t cksum = 0x55;
  for (uint8_t i = 0; i < 4; i++) {
    cksum += buf[i];
  }
  if (cksum != 0xff) {
    // invalid message!
    if (usart_txptr == 5) {  // don't respond unless we're not transmitting anything
      USART1->TDR = 0xfe;  // respond with a made-up NAK scheme
    }
  } else {
    for (uint8_t i = 0; i < 3; i++) {
      i2cdata_.bytes[i] = buf[i];
    }
    update_from_i2cdata();
  }
}

void USART1_IRQHandler(void) {
  uint32_t itflags = READ_REG(USART1->ISR);
  if (itflags & USART_ISR_TXE) {
    if (usart_txptr < 5) {
      USART1->TDR = usart_txbuf[usart_txptr++];
    } else {
      CLEAR_BIT(USART1->CR1, USART_CR1_TXEIE);
    }
  }
  if (itflags & USART_ISR_RXNE) {
    uint8_t chr = READ_REG(USART1->RDR);
    if (usart_rxptr >= sizeof(usart_rxbuf)) {
      usart_rxptr = -1;
    }
    if (usart_rxptr < 0 && chr == 0x55) {
      usart_rxptr = 0;
    } else if (usart_rxptr >= 0) {
      usart_rxbuf[usart_rxptr++] = chr;
      if (usart_rxptr == 4) {
        process_serial_msg(usart_rxbuf);
        usart_rxptr = -1;
      }
    }
  }
}

/* USER CODE END 4 */
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


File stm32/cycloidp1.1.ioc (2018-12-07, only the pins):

Mcu.UserName=STM32F030F4Px
PA0.Signal=GPXTI0
PA1.Signal=GPXTI1
PA10.Signal=I2C1_SDA
PA13.Signal=SYS_SWDIO
PA14.Signal=SYS_SWCLK
PA2.Signal=USART1_TX
PA3.Signal=USART1_RX
PA4.Signal=GPXTI4
PA5.Signal=GPIO_Output
PA6.Signal=S_TIM3_CH1
PA7.Signal=S_TIM3_CH2
PA9.Signal=I2C1_SCL
PB1.Signal=GPIO_Output
PF0-OSC_IN.Signal=RCC_OSC_IN
PF1-OSC_OUT.Signal=RCC_OSC_OUT

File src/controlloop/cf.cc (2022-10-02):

#include <stdio.h>
#include <sys/time.h>
#include <iostream>

#include <Eigen/Dense>

#include "hw/car/stm32rs232.h"
#include "hw/imu/imu.h"
#include "hw/input/js.h"
#include "inih/cpp/INIReader.h"

#include "controlloop/fit.h"
#include "controlloop/pid.h"
#include "controlloop/motorcontrol.h"

const int STEER_LIMIT_LOW = -85;
const int STEER_LIMIT_HIGH = 127;

const float WHEEL_DIAMETER = 0.065;
const float DRIVE_RATIO = 84./25. * 2.1;  // 84t spur, 25t pinion, 2.1 final drive
const float MOTOR_POLES = 3;  // brushless sensor counts per motor revolution
const float V_SCALE = WHEEL_DIAMETER*M_PI / DRIVE_RATIO / MOTOR_POLES;

using Eigen::Vector3f;
using Eigen::Matrix3f;

class CFIR : public JoystickListener, public ControlListener {
 public:
  CFIR(IMU *imu, JoystickInput *js) {
    imu_ = imu;
    js_ = js;
    js_throttle_ = 0;
    js_steering_ = 0;
    steertrim_ = 5;
    esctrim_ = 0;
    esctarget_ = 30;
    exit_ = false;
    recording_ = NULL;
    mode_ = Control;
  }
  virtual ~CFIR() {}

  virtual void OnButtonPress(char button) {
    switch (button) {
      case '+':  // plus button; start recording
        StartRecording();
        break;
      case '-':  // minus button; stop recording
        StopRecording();
        break;
      case 'L':
        esctrim_ = -127;
        break;
      case 'R':
        esctrim_ = esctarget_;
        break;
    }
  }

  virtual void OnButtonRelease(char button) {
    switch (button) {
      case 'L':
      // fall through
      case 'R':
        esctrim_ = 0;
        break;
    }
  }

  virtual void OnDPadPress(char direction) {
    switch (direction) {
      case 'R':
        steertrim_ += 1;
        printf("Steer trim: %d\n", steertrim_);
        break;
      case 'L':
        steertrim_ -= 1;
        printf("Steer trim: %d\n", steertrim_);
        break;
      case 'U':
        esctarget_ += 1;
        printf("ESC target: %d\n", esctarget_);
        break;
      case 'D':
        esctarget_ -= 1;
        printf("ESC target: %d\n", esctarget_);
        break;
    }
  }

  virtual void OnAxisMove(int axis, int16_t value) {
    switch (axis) {
      case 1:  // left stick y axis
        js_throttle_ = -value;
        break;
      case 2:  // right stick x axis
        js_steering_ = value;
        break;
    }
  }

  void StartRecording() {
    if (recording_) {
      StopRecording();
    }
    char fnamebuf[256];
    snprintf(fnamebuf, sizeof(fnamebuf), "log-%ld.txt", time(NULL));
    recording_ = fopen(fnamebuf, "w");
    if (recording_ == NULL) {
      perror(fnamebuf);
      return;
    }
    // setlinebuf(recording_);
    fprintf(recording_, "# dt u_esc u_steer dw wperiod gx gy gz ax ay az\n");
    fprintf(stderr, "recording %s\n", fnamebuf);
  }

  void StopRecording() {
    if (recording_ == NULL) {
      return;
    }
    fclose(recording_);
    recording_ = NULL;
    fprintf(stderr, "stopped recording\n");
  }

  int16_t Throttle() { return js_throttle_; }
  int16_t Steering() { return js_steering_; }

  int16_t js_throttle_;
  int16_t js_steering_;
  int8_t steertrim_;
  int8_t esctrim_;
  int8_t esctarget_;
  bool exit_;
  FILE *recording_;

  bool was_learning = false;

  IMU *imu_;
  JoystickInput *js_;

  enum {
    SysId = 0,
    Control = 1
  } mode_;

  int n = 0;

  virtual bool OnControlFrame(CarHW *car, float dt) {
    Vector3f accel, gyro;

    js_->ReadInput(this);
    imu_->ReadIMU(&accel, &gyro);

    float ds, v;
    car->GetWheelMotion(&ds, &v);

    float u_esc = 0;
    float u_steer = 0;
    switch (mode_) {
      case SysId:
        {
          if (!was_learning) {
            fprintf(stderr, "starting system identification\n");
          }
          was_learning = true;
          break;
        }
      case Control:
        {
          break;
        }
    }

    u_steer = Steering() / 32768. / 4. + steertrim_ / 127.0;
    u_esc = Throttle() / 32768. / 4. + esctrim_ / 127.0;

    fprintf(stderr, "%4d %4d\r", (int) (u_steer*127), (int) (u_esc*127));
    fflush(stderr);

    if (!car->SetControls(n >> 4, u_esc, u_steer)) {
      fprintf(stderr, "SetControls returned false?\n");
    }

    if (recording_) {
      fprintf(recording_, "%0.3f %d %d %f %f %f %f %f %f %f %f %f %f\n",
          dt, Throttle(), Steering(), u_esc, u_steer, ds, v,
          gyro[0], gyro[1], gyro[2],
          accel[0], accel[1], accel[2]);
    }

    n++;
    return !exit_;
  }
};

/*
void controltest() {
  float target_v = (n & 256) ? 200 : 400;

  // observe effect of previous input and update model
  float v = 0;
  if (wperiod != 0) {
    v = 1.0e6 / wperiod;
  }

  // loop bandwidth
  const float Wc = 0.5 * 6.28;

  // initial PID constants just to kick-start it; they will quickly be overwritten
  float Kp = 0.05;
  float Ki = 10*0.05;
  float Kd = 0;

  if (v != 0 && last_v != 0) {
    float dvdt = (v - last_v) / dt;
    float d2vdt2 = (dvdt - last_dvdt) / dt;
    //Vector3f X(last_u[0], last_u[0]*v, v, 1);
    Vector3f X(v, dvdt, d2vdt2);
    //XTY *= 0.97;
    //XTX *= 0.97;

    XTY += X * last_u[0];
    XTX += X * X.transpose();

    Eigen::LDLT<Matrix3f> ALDLT = XTX.ldlt();
    Vector3f k = ALDLT.solve(XTY);
    Ki = Wc * k[0];
    Kp = Wc * k[1];
    Kd = Wc * k[2];
    printf("c1=%f c2=%f c3=%f Ki=%f Kp=%f Kd=%f\n", k[0], k[1], k[2], Ki, Kp, Kd);

    last_dvdt = dvdt;
  }

#if 0
  const float Kp = 5;
  float target_vdot = Kp * (target_v - v);
  if (k[0] < 1) k[0] = 1;
  if (k[1] > 0) k[1] = 0;
  if (k[2] > 0) k[2] = 0;
  if (k[3] > 0) k[3] = 0;
  float uu = (target_vdot - k[2]*v - k[3]) / (k[0] + k[1]*v);
#if 0
  float uu = 0;
  if (n & 32) {
    uu += 32 - (n & 31);
  } else {
    uu += n & 31;
  }
#endif
#endif

  float err = target_v - v;
  float derr = (err - last_err) / dt;
  ierr += err * dt;
  last_err = err;
  float uu = Kp*err + Ki*ierr + Kd*derr;

  int8_t u = clipf(uu, -127, 127);
  // if (target_vdot > 0 && u < 10) u = 10;
  if (!car.SetControls(n >> 4, u, 0)) {
    fprintf(stderr, "SetControls returned false?\n");
  }
  // printf("%0.3f wpos:%d wperiod:%d k:%f %f %f %f v:%f tv:%f vdot:%f uu:%f u:%d lu:%d\n", dt, wpos, wperiod, k[0], k[1], k[2], k[3], v, target_v, target_vdot, uu, u, last_u[0]);
  printf("%0.3f wpos:%d wperiod:%d v:%f tv:%f uu:%f ierr:%f u:%d lu:%d\n", dt, wpos, wperiod, v, target_v, uu, ierr, u, last_u[0]);

  n++;
  // printf("   %d %d %d %d\n", last_u[0], last_u[1], last_u[2], last_u[3]);
  for (int i = 0; i < ESC_DELAY-1; i++) {
    last_u[i] = last_u[i+1];
  }
  last_v = v;
#endif
}
*/
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

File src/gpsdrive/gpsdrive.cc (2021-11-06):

#include "gpsdrive/gpsdrive.h"

#include <sys/time.h>

#include <Eigen/Dense>
#include <algorithm>
#include <string>

#include "gpsdrive/config.h"
#include "hw/car/car.h"
#include "hw/gps/ubx.h"
#include "hw/imu/imu.h"
#include "hw/imu/mag.h"
#include "hw/input/js.h"
#include "inih/cpp/INIReader.h"
#include "inih/ini.h"
#include "ui/display.h"

float clamp(float x, float min, float max) {
  if (x < min) x = min;
  if (x > max) x = max;
  return x;
}

GPSDrive::GPSDrive(FlushThread *ft, IMU *imu, Magnetometer *mag,
                   JoystickInput *js, UIDisplay *disp)
    : flush_thread_(ft),
      imu_(imu),
      mag_(mag),
      js_(js),
      display_(disp),
      gyro_last_(0, 0, 0),
      gyro_bias_(0, 0, 0),
      gps_v_(0, 0, 0) {
  done_ = false;
  record_fp_ = NULL;
  js_throttle_ = 0;
  js_steering_ = 0;
  config_item_ = 0;
  ierr_k_ = 0;
  ierr_v_ = 0;
  brake_count_ = 0;
  last_v_ = 0;
  last_w_ = 0;
  last_target_k_ = 0;
  lat_ = lon_ = 0;
  numSV_ = 0;

  ye_ = psie_ = k_ = 0;
  autodrive_k_ = 0;
  autodrive_v_ = 0;

  navheading_ = 0;
  navheading_last_ = 0;
  heading_ = 0;
  heading_init_ = false;
  heading_rollover_ = 0;

  control_hist_ptr_ = 0;
  state_hist_ptr_ = 0;

  autodrive_ = false;
  x_down_ = y_down_ = false;
  pthread_mutex_init(&record_mut_, NULL);
}

void* GPSDrive::gpsThread(void* arg) {
  GPSDrive *drive = (GPSDrive*)arg;
  fprintf(stderr, "GPS receive thread started\n");
  ubx_read_loop(drive->ubx_fd_, drive);
  return NULL;
}

bool GPSDrive::Init(const INIReader &ini) {
  if (config_.Load()) {
    fprintf(stderr, "Loaded driver configuration\n");
  }

  ubx_fd_ = ubx_open();
  if (ubx_fd_ == -1) {
    return false;
  }

  if (pthread_create(&gps_thread_, NULL, GPSDrive::gpsThread, (void*) this)) {
    perror("pthread_create");
    return false;
  }

  ref_lat_ = ini.GetInteger("nav", "reflat", 0);
  ref_lon_ = ini.GetInteger("nav", "reflon", 0);
  if (ref_lat_ == 0 || ref_lon_ == 0) {
    fprintf(stderr, "Please provide [nav] reflat and reflon in cycloid.ini\n");
    fprintf(stderr, "note: they are integers, w/ 7 decimal places\n");
    return false;
  }

  std::string trackfile = ini.GetString("nav", "track", "track.txt");
  if (!raceline_.LoadTrack(trackfile.c_str())) {
    return false;
  }

  // compute meters / 1e-7 degree on WGS84 ellipsoid
  // this is an approximation that assumes 0 altitude
  double invf = 298.257223563;                  // WGS84 inverse flattening
  double a = 6378137.0;                         // meters
  double b = a * (1 - 1/invf);
  double lat = ref_lat_ * M_PI * 1e-7 / 180.0;  // lat/lon in radians
  double clat = cos(lat);

  mscale_lat_ = b * M_PI / 180.0e7;
  mscale_lon_ = a * clat * M_PI / 180.0e7;

  // draw UI screen
  UpdateDisplay();
  display_->UpdateStatus("GPSDrive started.");

  return true;
}

GPSDrive::~GPSDrive() {}

void GPSDrive::UpdateControls(float in_throttle, float in_steering,
                              bool radio_safe, const StateObservation &obs,
                              float dt, ControlOutput *out) {
  const float srv_off = 0.001f * config_.servo_offset;
  const float srv_ratio =
      100.f / (config_.servo_rate == 0 ? 100 : config_.servo_rate);
  const float srv_kI = 0.01f * config_.servo_kI;
  const float srv_kP = 0.01f * config_.servo_kP;

  float u_s = clamp(in_steering + srv_off, config_.servo_min * 0.01f,
                    config_.servo_max * 0.01f);

  if (!autodrive_ && in_throttle <= 0.05) {
    out->Set(2, in_throttle, u_s);
    if (in_throttle < -0.05) {
      brake_count_ = 10;
    }
    ierr_v_ = 0;
    ierr_k_ = 0;
    last_v_ = obs.vx;
    last_w_ = obs.w;
    return;
  }

  if (autodrive_ && !radio_safe) {
    if (in_throttle < -0.5) {
      autodrive_ = false;
    }
    out->Set(2, -1, 0);
    return;
  }

  float max_throttle = 1.0;
  float target_v = config_.speed_limit * 0.01 * clamp(in_throttle, 0.f, 1.f);
  // float target_k = u_steering;
  float target_k = -in_steering * 1;

  // if autodriving, override target velocity and steering
  if (autodrive_) {
    // joystick control only goes up to 0.8, so give it a little boost
    max_throttle = in_throttle * 1.3;
    target_v = clamp(autodrive_v_, 0, config_.speed_limit * 0.01f);
    target_k = autodrive_k_;
  }

  float kerr = 0;
  if (obs.vx > 1.0) {
    // use a delayed target_k here so we're comparing against the yaw it
    // induced last control frame

    // 1 = t*kerr*srv_kI
    // t = 1/(kerr * srv_kI)
    // set srv_kI to, like, 10 or so except w is a bit noisy
    // i think it's already set to 2?
    kerr = last_target_k_ - obs.w / obs.vx;
    ierr_k_ = clamp(ierr_k_ + dt * srv_kI * kerr, -0.5f, 0.5f);
  } else {
    ierr_k_ = 0;
  }

  u_s = clamp((target_k + srv_kP * kerr + ierr_k_) * srv_ratio + srv_off,
              config_.servo_min * 0.01f, config_.servo_max * 0.01f);

  float vgain = 0.01 * config_.motor_gain;
  float kI = 0.01 * config_.motor_kI;
  float verr = target_v - obs.vx;
  float u = vgain * verr + kI * (ierr_v_ + verr * dt);
  if (u > -1 && u < 1) {
    ierr_v_ += verr * dt;
  }
  if (target_v < obs.vx * 0.9) {
    u = clamp(u, -1.f, max_throttle);
  } else {
    u = clamp(u, 0.f, max_throttle);
  }
  out->Set(1, u, u_s);

  last_v_ = obs.vx;
  last_w_ = obs.w;
  last_target_k_ = target_k;
  if (u < -0.05) {
    brake_count_ = 10;
  }
}
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

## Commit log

2017-07-19 import phase 1
    [baseplate.scad, baseplate.stl, camholder.scad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]
2017-08-11 Add wheel encoder / servo feedback measurement
    also fix some bugs; e.g. heaviside was defined incorrectly
2017-08-12 smooth as butter now.
    still need to figure out what's wrong with the gyro updates.
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2017-08-20 add raspberry pi userland submodule so we can cross-compile
2017-08-21 add schematic pdf
    also make i2c pullups no-populate; we don't actually need or want them
    [cycloid.kicad_pcb, cycloid.sch]
2017-09-09 generate log-likelihood in python updates!
    very useful to get a number on how well the filter works.
    also, experimental code gen to support model-predictive control
2017-09-10 tweaked motor friction model...
    it still basically sucks, though.
2017-09-13 relay from birdseye view recordings
    no longer supports 320x140 U channel recordings
2017-09-14 adding rest of code
    need to fix build now
    [imu.cc, imu_log.cc]
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2017-09-14 add gerbers to github
    [cycloid-B.Cu.gbl, cycloid-B.Mask.gbs, cycloid-B.SilkS.gbo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]
2017-09-16 forgot to commit UI.
    added wheel encoder feedback
2017-09-16 add config save/load with A and B buttons
2017-09-26 recursive bayes filter localization
    using a "track curvature signature", we can find our position along the
    track, just by following along with the changes in centerline curvature.
2017-10-11 switch to Wii U Pro Controller
    every single problem I had with the moga 2 controller just... completely
    went away. this is a much better controller.
2017-10-11 race line following muahaha
    it... sort of... mostly... seems to work! need to add velocity control
    next, and replace my crappy motor control PID, and then i should be
    getting 5-second laps around this track.
    [controller.cc]
2017-10-13 blah. experiment declared a failure.
    [controller.cc]
2017-10-18 adjusted my track curvature localization stuff, motor control stuff
    works pretty well now, but not well enough to follow along smoothly on a
    race line. *but* it knows to brake for turns ahead of time, so that's
    something.
2017-10-21 reverted motor model
    localization kinda works
    can't see the yellow line though
    [controller.cc]
2017-11-18 fix bug w/ rounding in remap generation
    [controller.cc]
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2018-08-07 strip down all the crap from before; bare framework
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2018-08-09 first cut of traffic cone localization
    TODO: refine landmark locations, generate new landmarks, fine-tune
    landmark selection
2018-08-11 add basic particle filter version
    needs tuning; looking for an effective likelihood criterion
2018-08-11 particle filter tuning
    much happier with these parameters now
2018-08-14 Rao-Blackwellized particle filter
    Can recover cone locations from an empty initialization
    In this experiment here, the location of the first cone is fixed, just
    so that it lines up with the overhead map.
2018-08-17 find closest point / normal / curvature on track
2018-08-18 getting very close now.
    doesn't quite work, but it almost works. mostly a particle filter tuning
    problem.
    in fact it may work pretty well already on larger venues but in my
    backyard it gets immediately lost.
    [controller.cc]
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2018-08-24 control speed based on front/rear wheel speed difference
    tries to maintain an optimal slip ratio for the front tire (the point
    where lateral velocity should still = 0 but the front tire is no longer
    statically gripping). we'll see if this works.
    [controller.cc]
2018-10-10 fix coordinate frame mixups; add simulator
    now it at least works in theory, and should be tunable to work in
    practice.
    [controller.cc]
2018-10-11 config tweaks from offline review
    V_ALPHA needs to be larger; velocity estimates lag significantly. also,
    we need to prevent integrator windup on the motor.
    M_K1 cannot possibly be correct, given the simulations in
    controller_test.cc. Will need to re-model this, perhaps.
    [controller.cc]
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2018-11-07 draw track / localizer visualization over front camera
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2018-11-09 hobbyking Blaze R1 adapters / mounting plates
    [blazer1.scad]
2018-11-29 updated config for blazeR1 with new HAT board
    [blazer1.scad]
2018-11-30 ready for 2018/11/30 event @ Voyage
    - 16 bit wheel period from STM32 HAT
    - adjust accel filter on MPU-9250
    - adjust various coneslam python parameters to match blaze R1
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2018-12-04 code used on 2018/11/30 competition @ voyage.auto
    added / fixed per-particle heading stuff, but disabled it.
    [controller.cc]
2018-12-07 add STM32F030 code
    uses drivers from STM32CubeMX for now. I've found a lot of the HAL code
    to be useless in, e.g., actually implementing an I2C slave, so I may
    completely remove it, but for now it's convenient to do the device setup
    with STM32CubeMX.
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2018-12-08 add OpenOCD config and compiling / flashing instructions
    [raspberrypi2-native.cfg]
2018-12-08 deprecate teensy code
    the stm32 is a much better behaved i2c slave than the arduino wire
    library will ever be
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2018-12-08 failsafe: if host doesn't send an update within 100ms, stop motors
    [main.c]
2018-12-31 add STL files for Blaze R1 parts
    [blazer1-arducam.stl, blazer1-baseplate-rpionly.stl, blazer1-shocktowermount.stl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]
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2019-01-18 Readme: Update IMU reference and fix my earlier grammar mistake
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2019-01-21 code run during 2019/01/19 diyrobocars competition
    the servo code is a hack but less than it was before, i think?
2019-01-21 updated parameters on some random junk
    - improved the fiducial detection rate
    - tweaked particle filter noise params
2019-04-08 new blaze mounting design, camera pointing up
    [blazer1-rearup.scad]
2019-04-08 adjusted positioning and screw diameters
    [blazer1-rearup.scad]
2019-04-12 blaze r1 updates
    [blazer1-rearup.scad, lcdstand.scad]
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2019-04-12 improve design of lcd riser
    [lcdstand.scad]
2019-04-13 add Exceed Magnet mounting design
    [magnet.scad]
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2019-04-16 coneslam 360, totally hacked together on the C++ code side
    [magnet.scad]
2019-04-18 fix some bugs in localization; use IFF export format
    adds more datalogging, with each datalog chunk as an IFF chunk. so now
    the file is fully self-delimiting.
    [controller.cc]
2019-04-19 turned the camera 90 degrees, rebuilt tables... retuned a bunch of stuff
    [magnet.scad]
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2019-04-21 rotate camera 45 degrees
    wish i had thought of this sooner
    [blazer1-rearup.scad]
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2019-04-26 new motor / servo control stuff
    parameters are not quite right yet but it mostly works... however it
    still lacks the one thing i need, which is a yaw error term in the motor
    control
    [cf.cc, controller.cc]
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2019-04-27 compile fix, add turn-in brake
    [cf.cc, controller.cc]
2019-04-28 fix compile error, also insane curvatures in controller
    [controller.cc]
2019-05-01 minor tool changes
    - trackplan can load older format
    - 2-parameter motor model fit rather than 3 (less likely to blow up)
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2019-05-10 new value function driving thing
    might be working, not sure. fixed known bugs, can't test until tomorrow.
    [controller.cc]
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2019-05-26 first cut "bundle adjustment"
    although it's not that, yet, it's just a one-pass ceiling recovery
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2019-07-01 fixes and updates from circuit launch 2019/06/29 race
    [controller.cc]
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2019-07-07 attempt 1: windshield camera mount
    [blazer1-windshield.scad, blazer1-windshield.stl]
2019-07-07 moved camera down a smidge
    [blazer1-windshield.scad, blazer1-windshield.stl]
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2019-07-20 new magnet mounting
    [magnet.scad]
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2019-08-02 checkpoint: fixing a bunch of crap under a time crunch
    [controller.cc]
2019-08-03 hack valueiter to have correct track width and do regular checkpoints
2019-08-06 fix major bug in speed control
    [controller.cc]
2019-08-08 switch back to regular gain-scheduled PI control
    previous PD transform was a flawed idea.
2019-08-12 fix replay with new control cost logging; also add lap timer
2019-08-12 8/11/2019 back-to-school testing
    - switch from Wii U controller to Logitech F710
    - plan assuming car continues for 60-90ms before control action is
    taken
    - test lots of curvature options, not just ones around current
    curvature.
    - log car config immediately on opening a recording file
2019-08-13 whoops, wrong C++ cast
    [controller.cc]
2019-08-19 fixing some extra junk
    [cf.cc, driver.cc]
2019-09-14 fix a bunch of steering/driving configurability bugs
    [controller.cc, driver.cc, main.cc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]
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2019-09-16 add obstacle detector and plumb data to planner
    planner doesn't use it as a penalty, yet
    [controller.cc, driver.cc, main.cc]
2019-09-19 fix some stuuuupid bugs in IMU velocity estimation
    [driver.cc]
2019-09-19 fix bugs w/ cone dodging
    [controller.cc, driver.cc]
2019-09-20 fix UI bug, zero-curvature bug, add new param
    [controller.cc]
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2019-12-04 some UI fixes + starting on 4d value function + PyCUDA value iteration
    [driver.cc]
2019-12-05 added collision penalties to cost
    [controller.cc]
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2019-12-06 more minor tweaks to vicuda
    what should work, but doesn't seem to, is to set the timestep only large
    enough to get to the next grid tile, instead of something huge like 125
    milliseconds. I'm not sure why.
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2019-12-13 UI tweaks, planner / control fixes
    - show camera view and front view on UI
    - raise accelerometer bandwidth to ~50Hz
    - follow yaw rate in lookahead (was assuming understeering before)
    [controller.cc, driver.cc, invensense.cc]
2019-12-13 bugfixes for front table lookup; also test motor freewheeling
    [motorlearn.cc]
2019-12-19 new fisheye model code; computes lookup tables from camera intrinsics
    still need to update the drive code and provide camera configs, fix test
    data
2019-12-19 fix ARM NEON code for fixed point LUT
2020-02-13 get rid of fp16 stuff; use int16 fixed point and local fisheye model
    [controller.cc, driver.cc, main.cc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]
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2020-02-21 minor fixes, actually works now
    [gpsdrive.cc]
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2020-02-25 bugfixes from track day
    [gpsdrive.cc]
2020-02-26 add STL for blaze R2 raspi mount
    [blazer1-rpimount.stl]
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2020-03-02 accidental dependency on lens for gpsdrive
    i probably won't bother to fix this ever
2020-03-05 add steering-error proportional term
    [controller.cc]
2020-03-05 add kP steering-error control for gpsdrive as well
    [gpsdrive.cc]
2020-12-07 add a bunch of 3d-printed mounting stuff for various cars
    - Exceed Magnet RPi, camera, LCD riser
    - Quantum Vandal RPi, camera+bumper
    - WlToys K989 w/ Raspberry Pi Zero
    [k989.scad, k989.stl, magnet-camera.stl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]
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2021-05-21 hack hack hack hack hack hack
    [blazer1-windshield.scad]
2021-05-23 some bugfixes/improvements, mostly dirty hacks
    This is the code that ran the 2021-05-22 race.
    [controller.cc, driver.cc]
2021-05-23 adding new circuit launch maps
    the svg is drawn in inkscape to define the track centerline
2021-08-17 Various fixes to make stuff work again; also added fps counter
    [controller.cc, driver.cc]
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2022-10-05 add smoothness + understeer penalties
    also explicitly sample from both starting lanes

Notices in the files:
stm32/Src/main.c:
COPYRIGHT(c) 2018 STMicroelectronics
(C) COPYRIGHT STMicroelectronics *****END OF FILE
